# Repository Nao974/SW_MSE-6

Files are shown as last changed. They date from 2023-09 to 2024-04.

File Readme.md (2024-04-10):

# Mouse Droid MSE-6 StarWars

En collaboration avec l'association [Les Voyageur Des Etoiles] réalisation d'une réplique du **Mouse Droid MSE-6** des films **StarWars** :

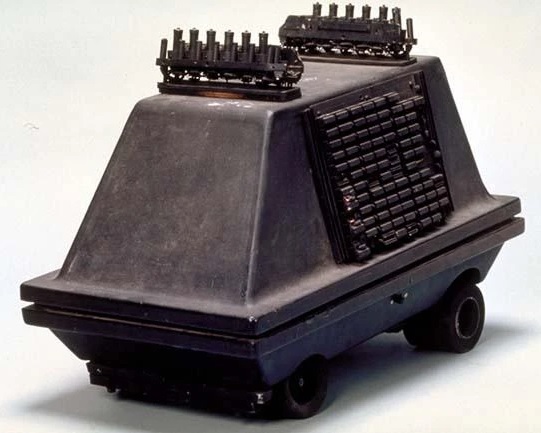
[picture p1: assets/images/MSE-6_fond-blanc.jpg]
Image du Robot
 

*Conçu et produit par Rebaxan Columni pour le compte de l'Empire. De petite taille (moins de 30cm de hauteur), il est muni de quatres roues. Ce modèle est utilisé pour les tâches de maintenance simples et pour le nettoyage des sols.*

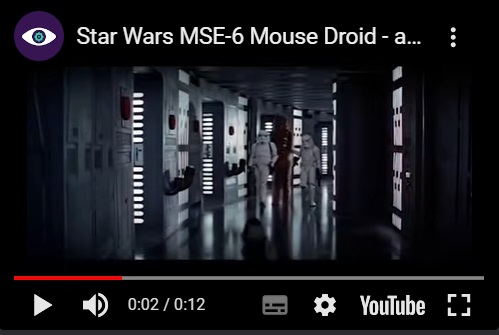
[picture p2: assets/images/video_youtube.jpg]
Video Presentation (https://youtu.be/cLqNmMH4hsg)


L'objectif du projet est d'avoir un robot pilotable par Smartphone permettant d'accompagner les acteurs dans leurs déambulations lors de salons ou d'animations.

Ce robot doit également avoir une fonction "Autonome" lui permettant de déambuler seul dans un endroit clos en évitant les obstables.

* Dimension à l'échelle 1
* Modes de fonctionnement
    * Pilotage en BlueTooth sur Android
    * Mode autonome aléatoire avec detection d'obstacles
    * Ne doit pas être très rapide car déplacement dans la foule
* Sur batterie avec une autonomie d'au moins 20 minutes
* Eclairage d'ambiance par ruban à LED
* Bruitage sonore MP3 tirés du film

# Dimensions
Plan issu du site http://luckyxero.com/droids/mouse-droid-build/ *(dimensions en inches)*

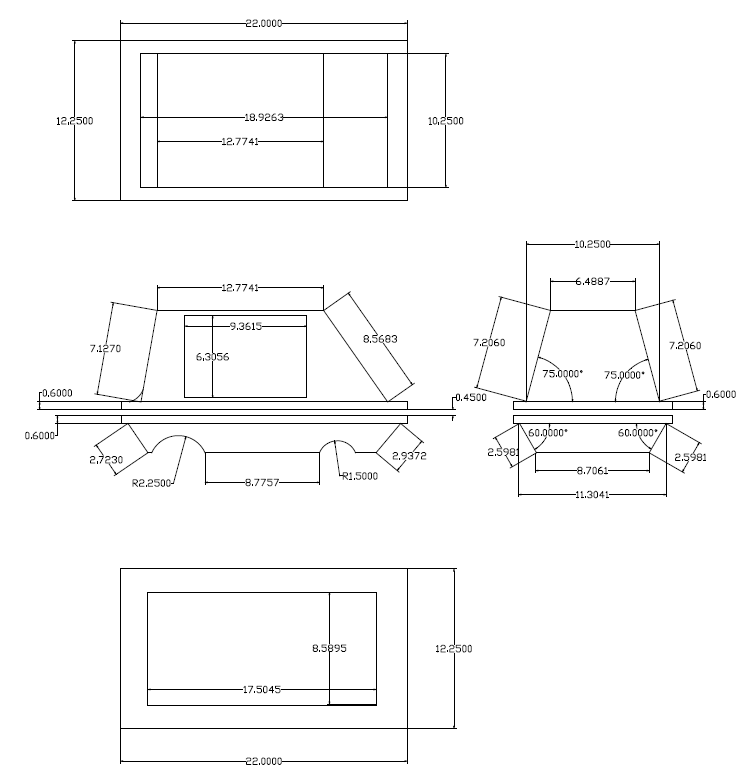
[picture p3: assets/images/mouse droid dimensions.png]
Dimension


# Construction

La coque a été fabriquée avec :
*  du carton-plume de 6 mm d'épaisseur,
* recouvert de plusieurs couches de vernis epoxy
* Peinture noire
* Décoration sur le dessus : http://www.thingiverse.com/thing:1862673
* Décoration sur les côtés : https://www.thingiverse.com/thing:916594

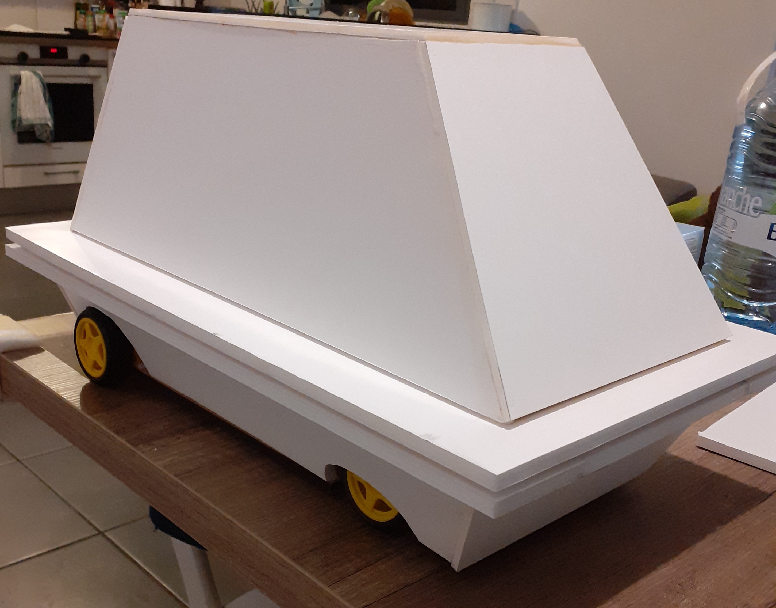
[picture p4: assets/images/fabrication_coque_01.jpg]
Construction carton plume


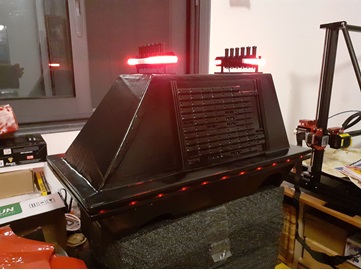
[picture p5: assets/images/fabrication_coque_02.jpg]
Avec les LEDs


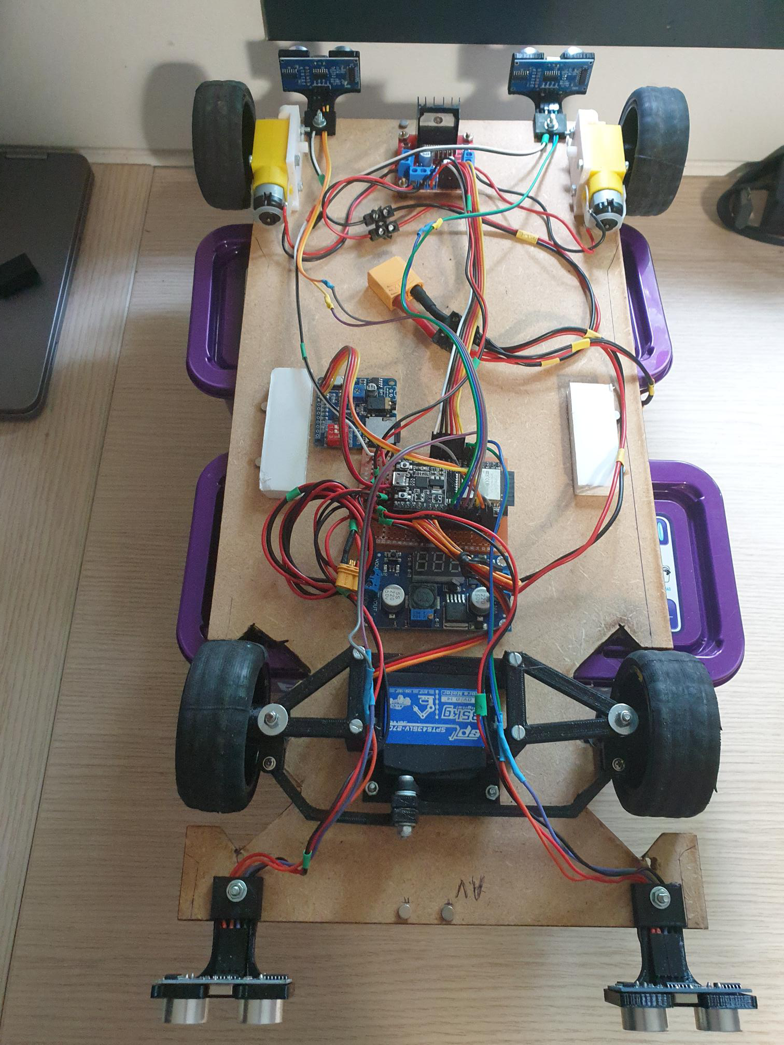
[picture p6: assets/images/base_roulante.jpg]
Base Roulante


# Pilotage par Smartphone

Télécharger l'application Android [apk]

Vous pouvez également ouvrir le projet directement dans [MIT App Inventor]

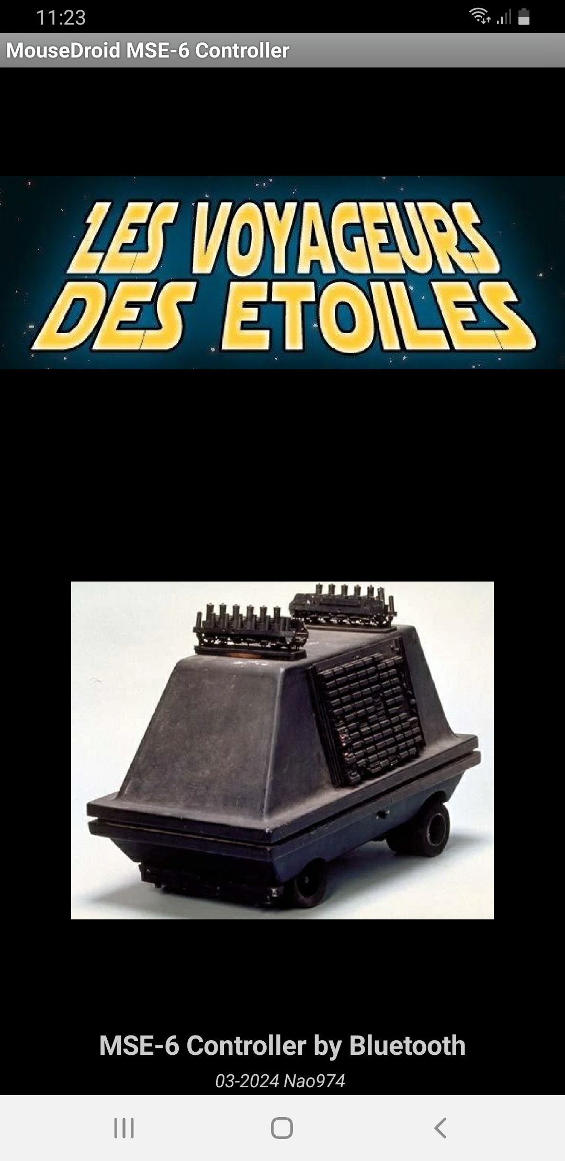
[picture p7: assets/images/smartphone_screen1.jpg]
Splash Screen
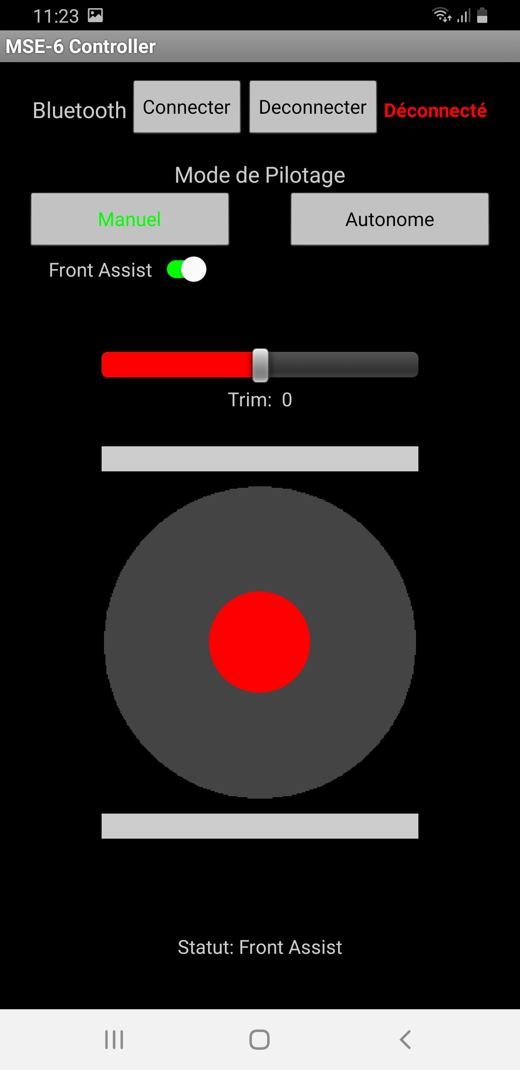
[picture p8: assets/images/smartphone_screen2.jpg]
Mode Manuel
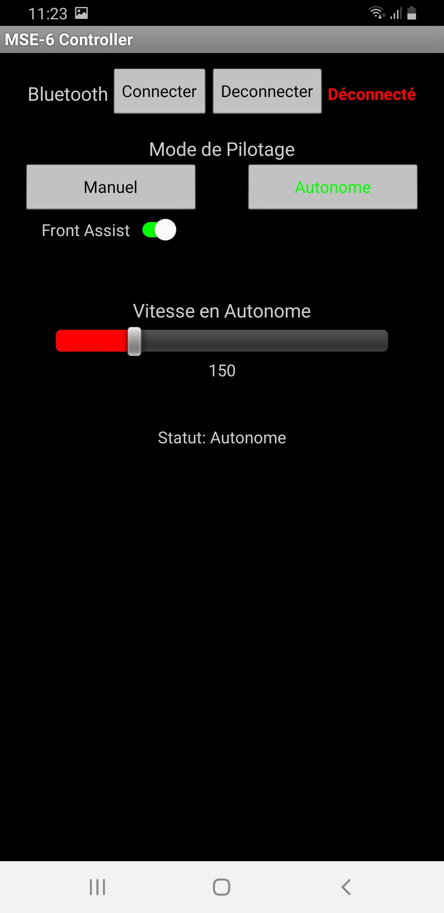
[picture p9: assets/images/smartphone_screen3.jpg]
Mode Autonome
<div align="center">&nbsp;&nbsp;</div> 

# Vidéos diverses

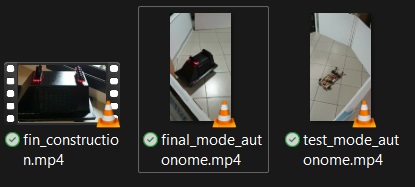
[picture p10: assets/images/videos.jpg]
Divers Vidéos


# 
*[Nao974] v1.0 2024-04*

[FICHES]: ./FICHES
[apk]: ./android_apk/MouseDroid_MSE6.apk
[MIT App Inventor]: https://gallery.appinventor.mit.edu/?galleryid=becb1436-0f10-454d-a0c5-cfbd2a7cbcf6

[Robotic974]:      https://www.facebook.com/robotic974
[Nao974]:          https://www.youtube.com/@Nao974Robotic
[Les Voyageur Des Etoiles]: https://www.facebook.com/LesVDE
[Images de référence] :     https://photos.google.com/share/AF1QipP5TdWiDbklsdGn5iPU7iJ0s8NH2A8It0JS8Ncwk7ek5rMM8T10t8TtdKYRnrsGPw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

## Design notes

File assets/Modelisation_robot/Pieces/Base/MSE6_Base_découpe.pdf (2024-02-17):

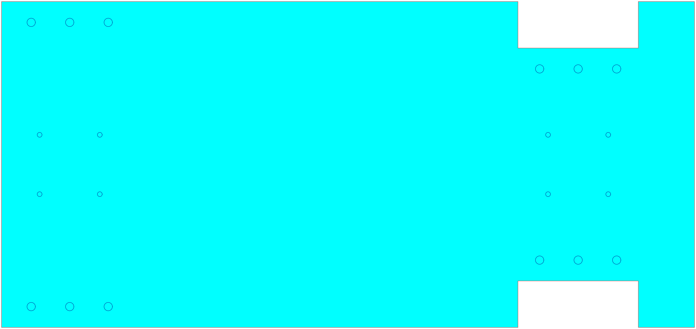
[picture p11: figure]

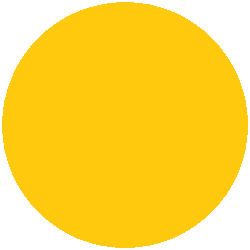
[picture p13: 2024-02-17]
assets/images/fondStickb.png

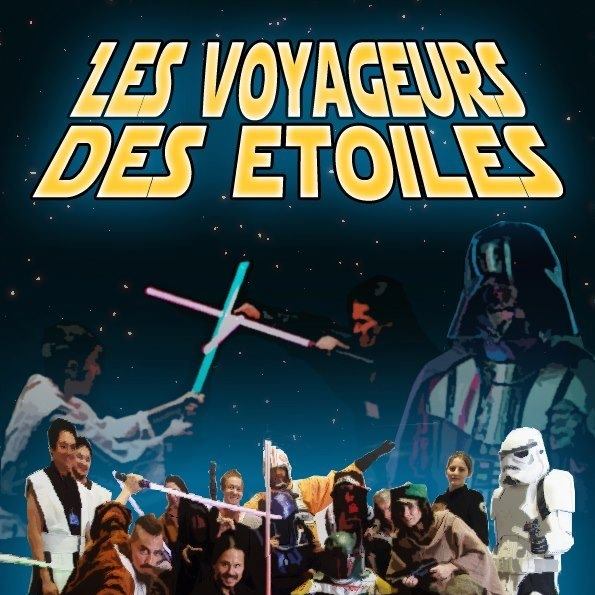
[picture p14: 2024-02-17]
assets/images/Voyageur_Etoiles.jpg

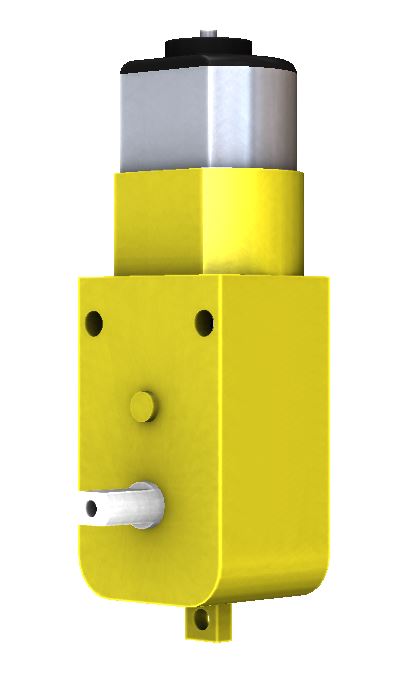
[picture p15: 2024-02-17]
assets/Modelisation_robot/Pieces/_tt-motor/motor.JPG

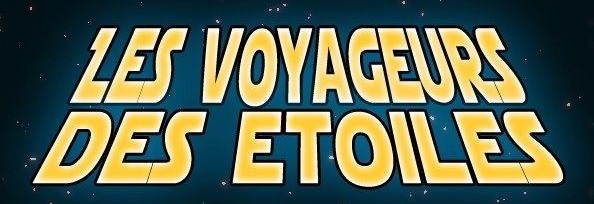
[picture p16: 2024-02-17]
assets/images/Voyageur_Etoiles_texte.jpg

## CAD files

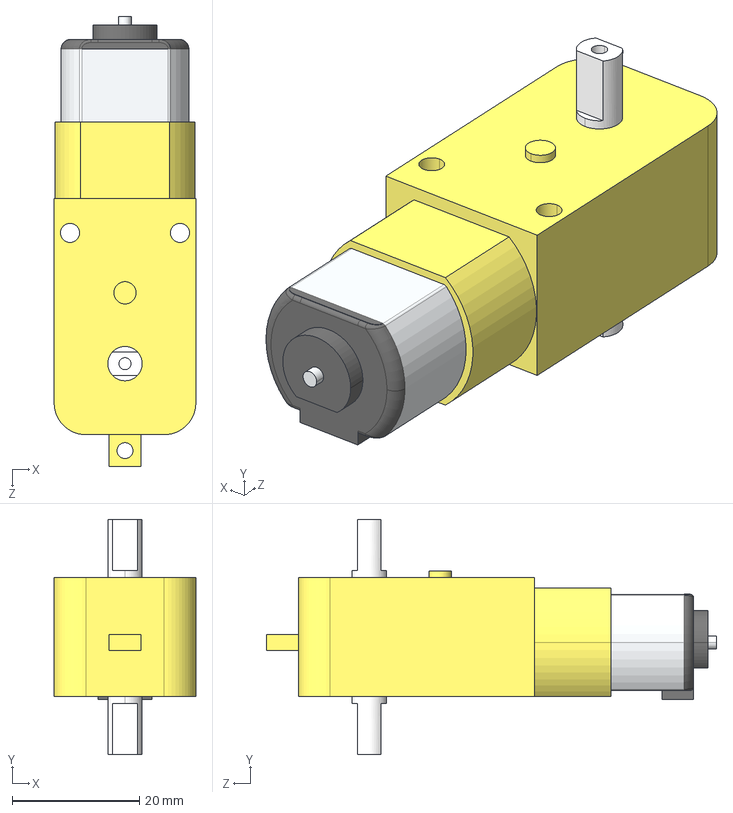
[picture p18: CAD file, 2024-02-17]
assets/Modelisation_robot/Pieces/_tt-motor/motor.STEP
22.3 x 37.0 x 70.8 mm

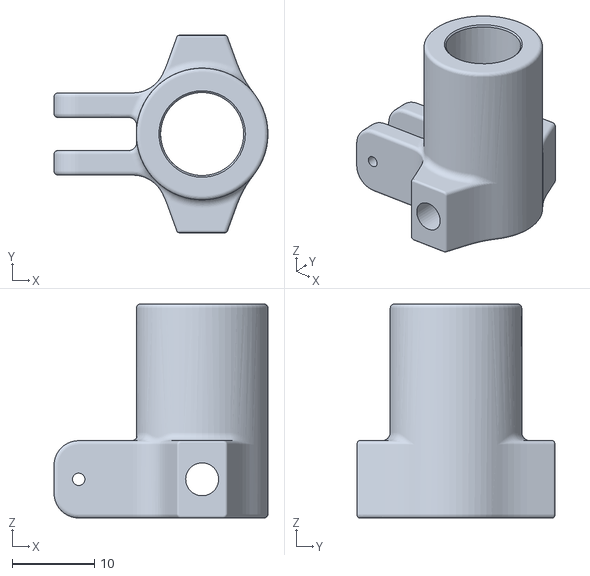
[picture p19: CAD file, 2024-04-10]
assets/Modelisation_robot/Pieces/Direction/Hub_front.STL
26.0 x 24.0 x 26.0

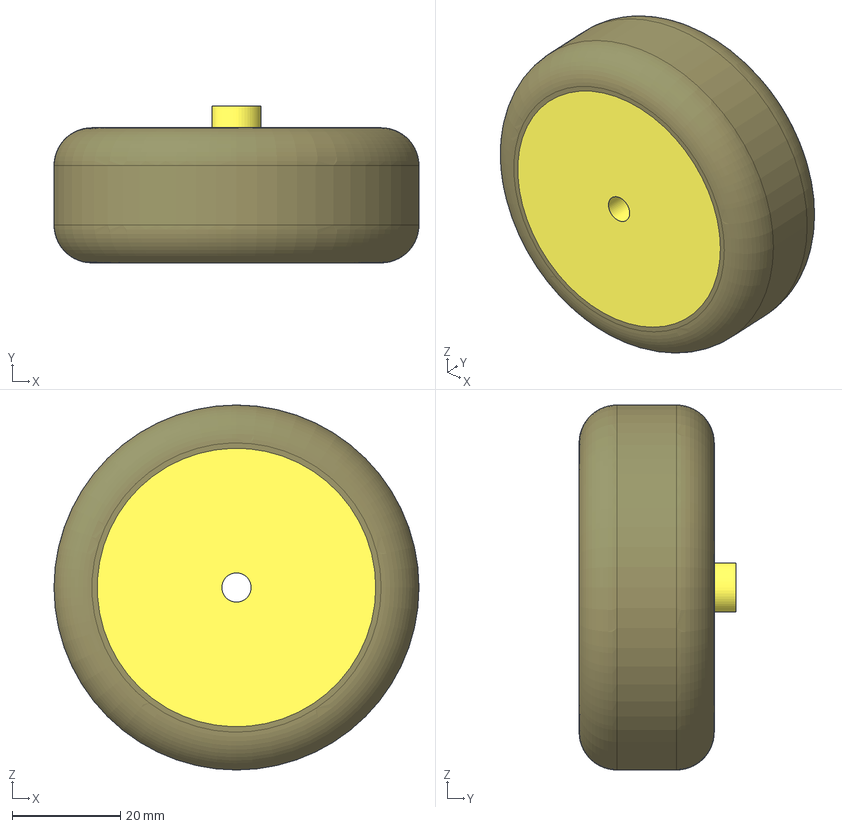
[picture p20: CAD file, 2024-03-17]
assets/Modelisation_robot/Pieces/Roue/Roue.FCStd
67.5 x 29.0 x 67.5 mm
Jante
Pneu
Binder(Roue)

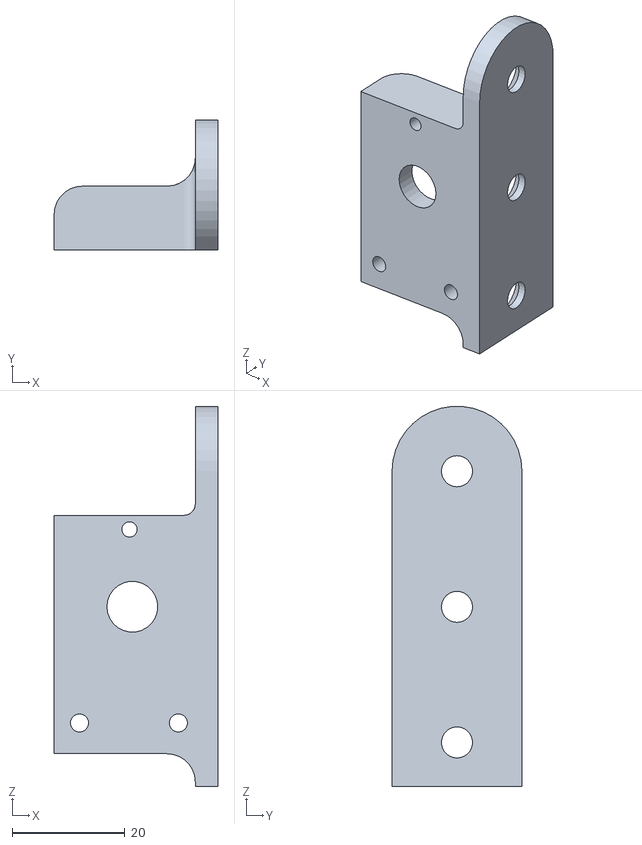
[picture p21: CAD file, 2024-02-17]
assets/Modelisation_robot/Pieces/Support_Moteur/Support_Moteur_gauche.stl
29.0 x 23.0 x 67.3

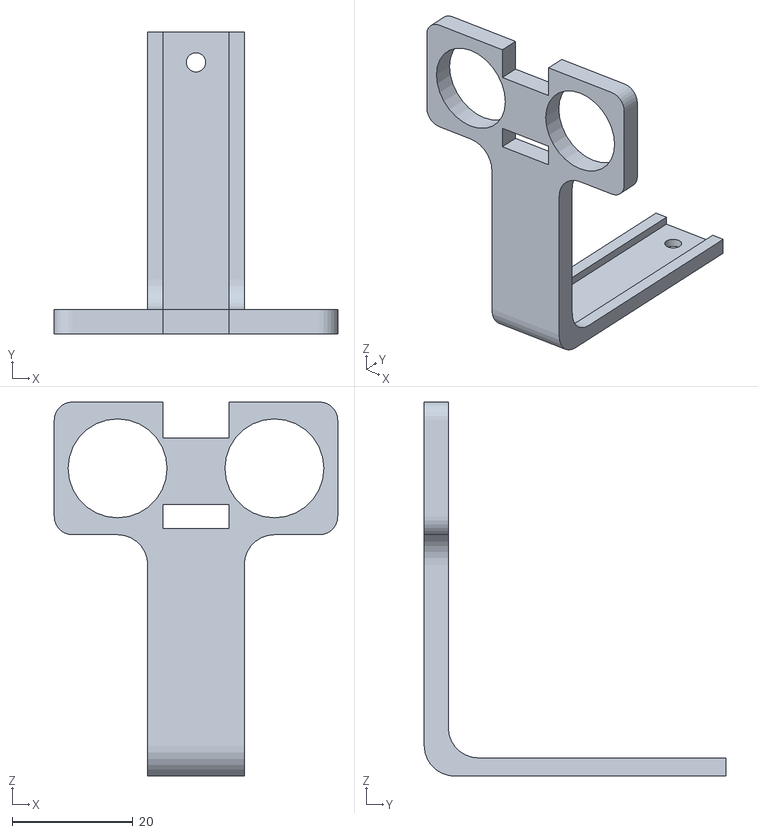
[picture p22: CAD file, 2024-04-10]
assets/Modelisation_robot/Pieces/Ultrasonic HC-SR04/support_HC-SR04_haut_arriere-Support.stl
47.0 x 50.0 x 62.0

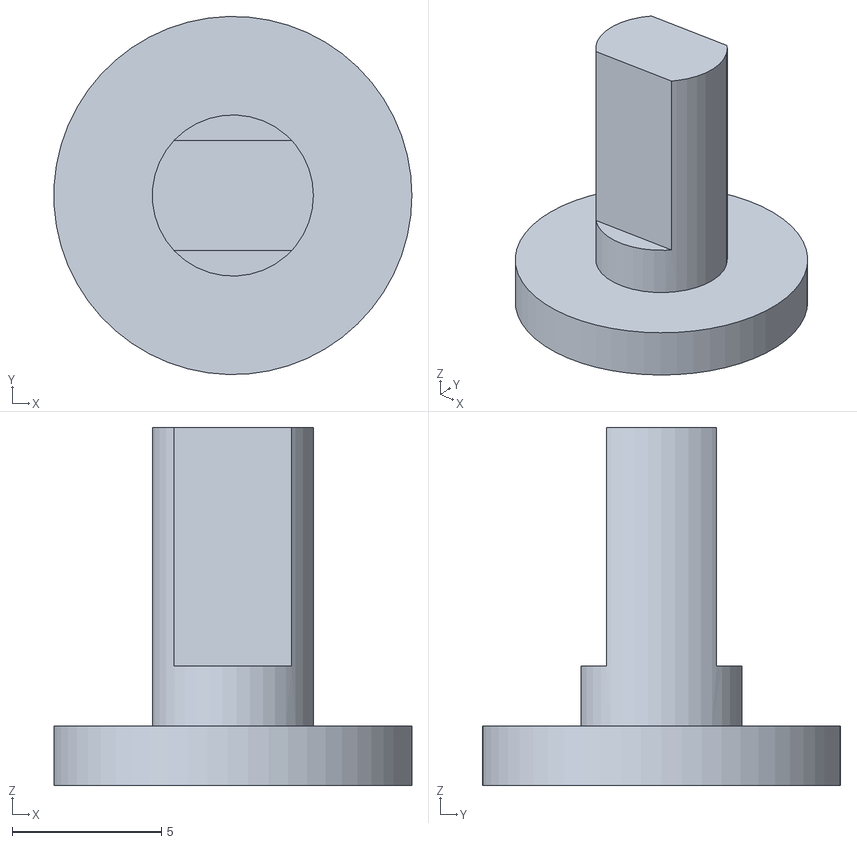
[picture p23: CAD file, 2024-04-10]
assets/Modelisation_robot/Pieces/Direction/driveshaft_front.STL
12.0 x 12.0 x 12.0

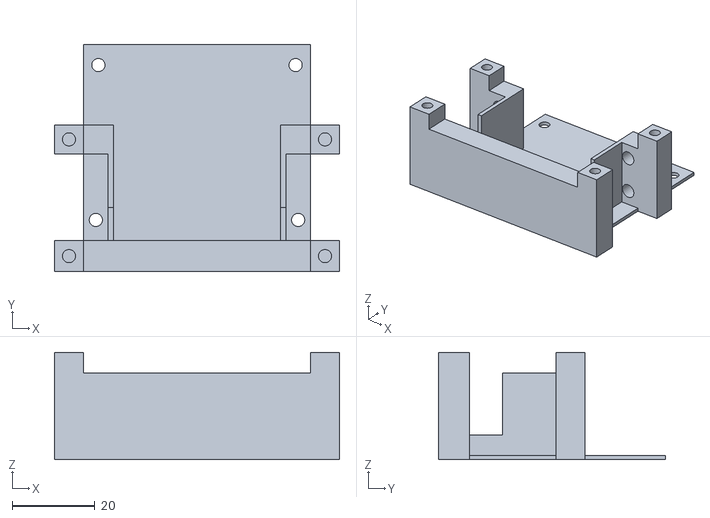
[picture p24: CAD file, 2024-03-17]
assets/Modelisation_robot/Pieces/Direction/support_servo-Body.stl
69.0 x 55.0 x 26.0

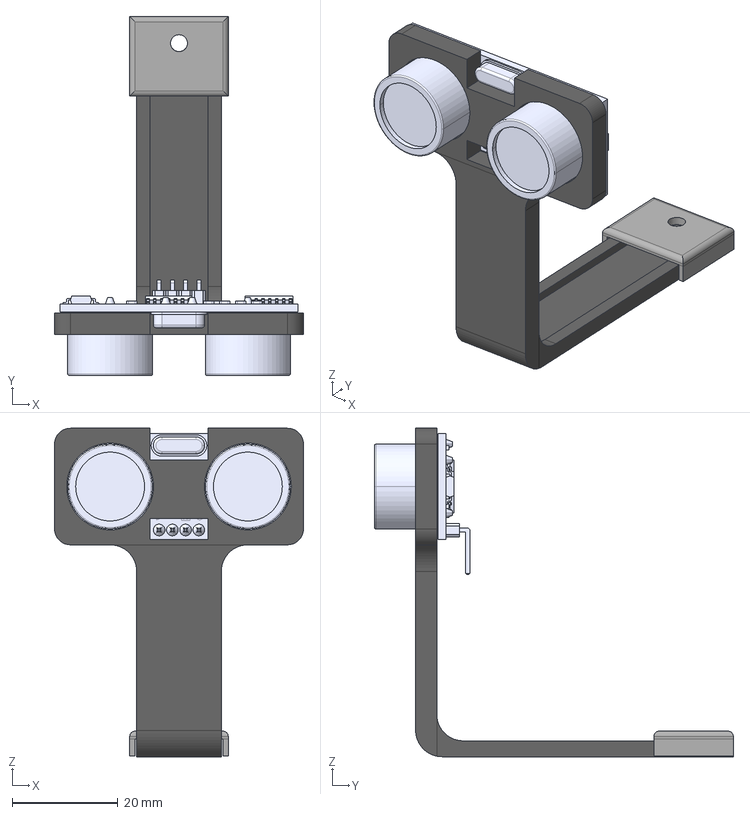
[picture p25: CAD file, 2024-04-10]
assets/Modelisation_robot/Pieces/Ultrasonic HC-SR04/support_HC-SR04_haut.FCStd
47.0 x 67.8 x 62.0 mm
Support
HCSR04 Ultrasonic Sensor
Capot vis

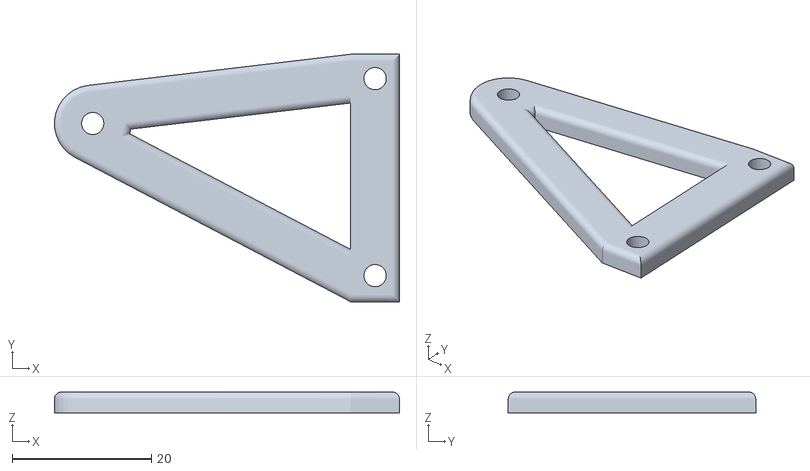
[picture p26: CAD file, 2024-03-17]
assets/Modelisation_robot/Pieces/Direction/Triangle_Gauche.stl
49.5 x 35.5 x 3.00

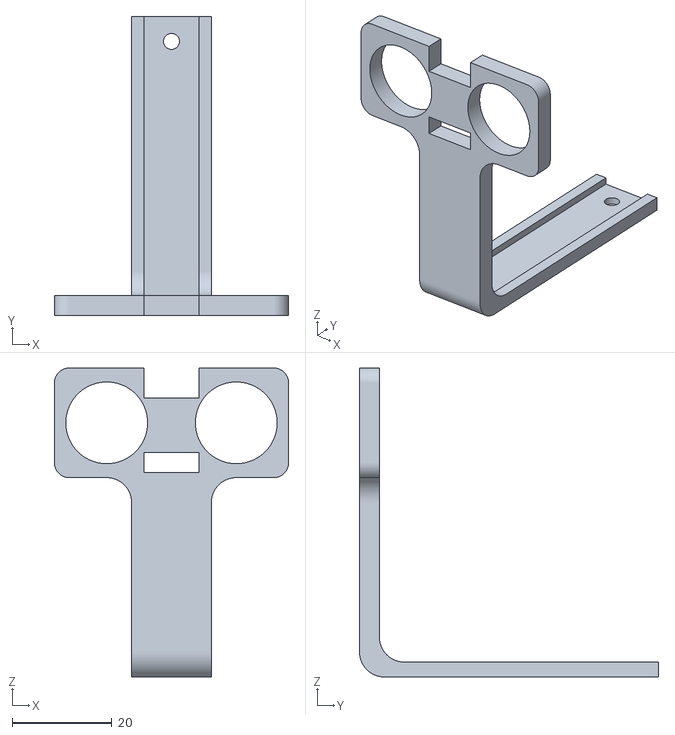
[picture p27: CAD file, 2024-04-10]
assets/Modelisation_robot/Pieces/Ultrasonic HC-SR04/support_HC-SR04_haut-Support.stl
47.0 x 60.0 x 62.0

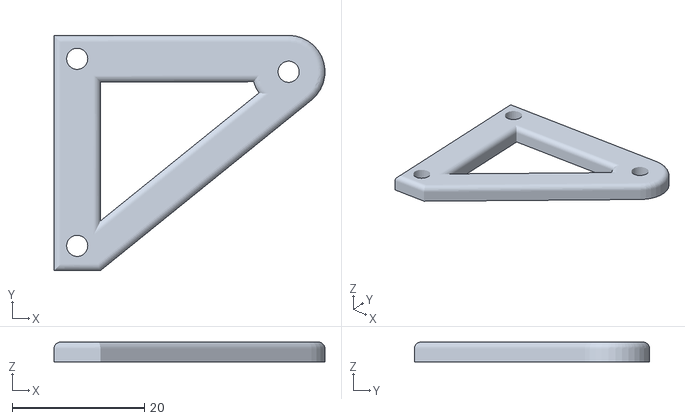
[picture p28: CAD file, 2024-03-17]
assets/Modelisation_robot/Pieces/Direction/Triangle_Droit.stl
40.9 x 35.5 x 3.00

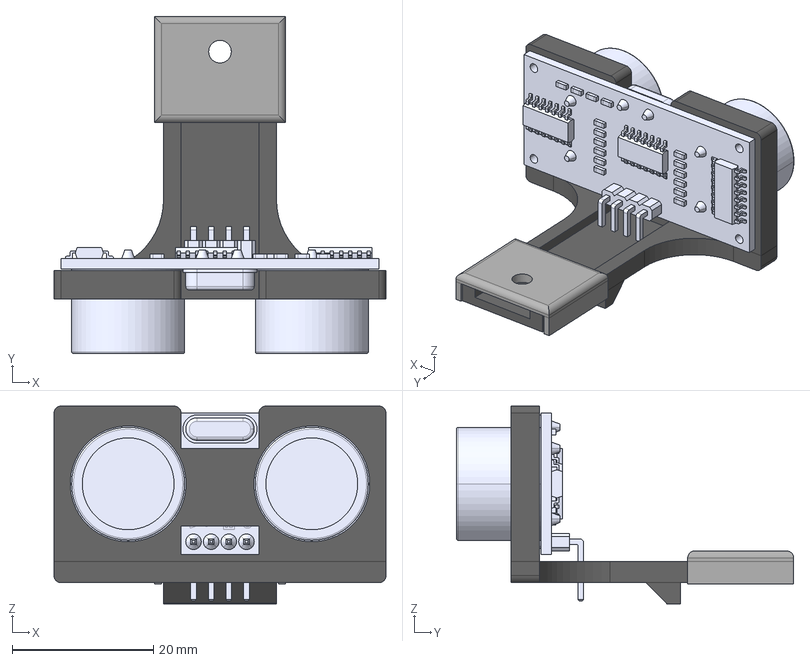
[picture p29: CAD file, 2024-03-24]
assets/Modelisation_robot/Pieces/Ultrasonic HC-SR04/support_HC-SR04_court.FCStd
47.0 x 47.8 x 28.0 mm
Support
HCSR04 Ultrasonic Sensor
Capot vis

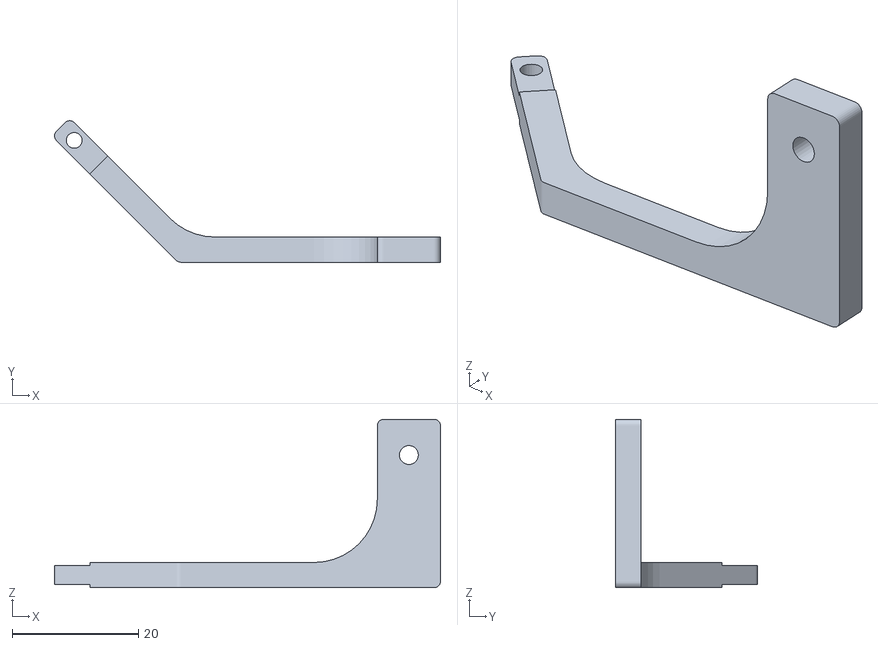
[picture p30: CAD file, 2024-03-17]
assets/Modelisation_robot/Pieces/Direction/Bras_Droit-Body.stl
61.1 x 22.4 x 26.7

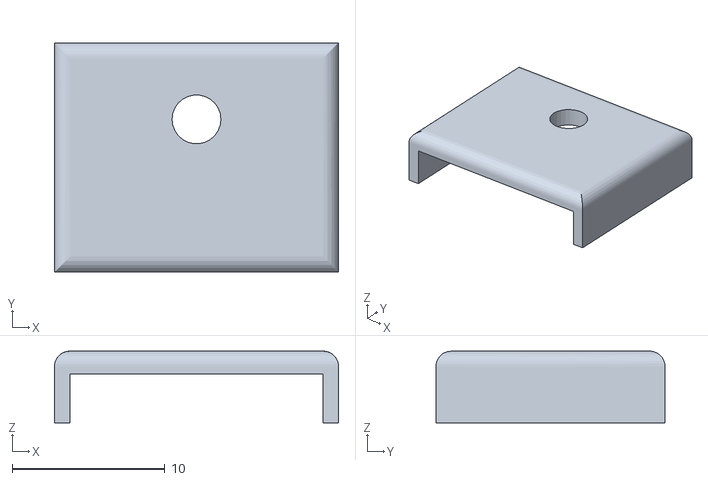
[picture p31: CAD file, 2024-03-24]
assets/Modelisation_robot/Pieces/Ultrasonic HC-SR04/support_HC-SR04_Capot vis.stl
18.6 x 15.0 x 4.70

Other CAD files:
assets/Modelisation_robot/Pieces/Support_Moteur/Support_Moteur.FCStd
assets/Modelisation_robot/Pieces/Ultrasonic HC-SR04/support_HC-SR04_haut_arriere.FCStd
assets/Modelisation_robot/Pieces/Direction/support_servo.FCStd
assets/Modelisation_robot/Pieces/Ultrasonic HC-SR04/support_HC-SR04.FCStd
assets/Modelisation_robot/Pieces/Direction/Bras_Droit.FCStd
assets/Modelisation_robot/Pieces/Direction/Bras_Gauche-Body.stl
assets/Modelisation_robot/Pieces/Direction/Bras_Gauche.FCStd
assets/Modelisation_robot/Pieces/Ultrasonic HC-SR04/HCSR04 Ultrasonic Sensor.STEP
assets/Modelisation_robot/Pieces/_tt-motor/motor.STL

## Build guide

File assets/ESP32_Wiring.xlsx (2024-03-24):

 | GPIO0 | Boot
 | GPIO1 | TX1
 | GPIO2
 | GPIO3 | RX1
 | GPIO4 | Servo Motor Direction
 | GPIO5
 | GPIO6 | Reserved SPI Flash
 | GPIO7 | Reserved SPI Flash
 | GPIO8 | Reserved SPI Flash
 | GPIO9 | Reserved SPI Flash
 | GPIO10 | Reserved SPI Flash
 | GPIO11 | Reserved SPI Flash
 | GPIO12 | Right Motor ENA
 | GPIO13
 | GPIO14 | Right Motor IN1
 | GPIO15
 | GPIO16 | US Left Back Echo
 | GPIO17 | US Left Back Trigger
 | GPIO18 | US Right Back Echo
 | GPIO19 | US Right Back Trigger
 | GPIO20
 | GPIO21 | MP3RX2
 | GPIO22 | MP3TX2
 | GPIO23 | US Right Front Trigger
 | GPIO24
 | GPIO25 | Left Motor IN2
 | GPIO26 | Left Motor IN1
 | GPIO27 | Right Motor IN2
 | GPIO28
 | GPIO29
 | GPIO30
 | GPIO31
 | GPIO32 | US Left Front Trigger
 | GPIO33 | Left Motor ENA
Input Only | GPIO34 | US Left Front Echo
Input Only | GPIO35 | US Right Front Echo
Input Only | GPIO36
 | GPIO37
 | GPIO38
Input Only | GPIO39

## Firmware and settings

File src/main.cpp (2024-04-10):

#include <Arduino.h>

// General
uint8_t drivingMode = 1, autonomousState= 1, autonomousStateLast= 1;
int16_t vitesseAutonomous;
uint32_t debugLastMillis, autonomousLastMillis, autonomousWaitLastMillis, autonomousWait;
#define DEBUG	false

#include "DYPlayerArduino.h"
const uint8_t MP3RX2 = 22;
const uint8_t MP3TX2 = 21;
DY::Player player(&Serial2);

#include "BluetoothSerial.h"
BluetoothSerial SerialBT;
int16_t btReceive[4] = {0, 0,  0, 0}; // Pilotage,  Trim, Joy X / Range Left, Joy Y / Range Right 

#include <L298N.h>
Moteur moteurGauche, moteurDroite;
int16_t vitesseBase;
int16_t reculeDuree;
int32_t reculeLastMillis;

#include "Direction.h"
#include <ESP32Servo.h>
Servo servoDir;
int16_t directionBase;

#include "Sonars.h"
#include <NewPing.h>
uint8_t sonarStatus[SONAR_NUMBER]= {0, 0, 0, 0};
NewPing sonar[SONAR_NUMBER]= {
    NewPing( 32, 34, SONAR_MAX_DISTANCE),  // Left Front sensor (trigger pin, echo pin, and max distance to ping).
    NewPing( 17, 16, SONAR_MAX_DISTANCE),  // Left Back
    NewPing( 23, 35, SONAR_MAX_DISTANCE),  // Right Front
    NewPing( 19, 18, SONAR_MAX_DISTANCE)  // Right Back
};

void setup() {
// Initialization of Serial debug
    #if DEBUG== true 
		Serial.begin(115200);
	#endif

// Initilization of the Bluetooth server
	#if DEBUG== true 
		Serial.println("SerialBT init"); 
	#endif
    SerialBT.begin("MSE-6");

// Initialization of motors
	#if DEBUG== true 
		Serial.println("Motors init"); 
	#endif
	moteurGauche.init(26, 25, 33, VITESSE_MAX); // IN1, IN2, ENA
	moteurDroite.init(14, 27, 12, VITESSE_MAX); // IN1, IN2, ENA
	vitesseBase = 0;

// Initialization Direction
	#if DEBUG== true 
		Serial.println("Servo init"); 
	#endif
	servoDir.attach(4, 1000, 2000);
	directionBase = 90;
	servoDir.write(directionBase);

// Initialization Sonars
	#if DEBUG== true 
		Serial.println("Sonars init"); 
	#endif
    sonarID = 0;
    sonarLastMillis = millis();

// Initialization MP3 Player
  Serial2.begin(9600, SERIAL_8N1, MP3RX2, MP3TX2);
  player.begin();
  player.setVolume(25); //Set the playback volume between 0 and 30. Default volume if not set: 20
  player.setCycleMode(DY::PlayMode::Random); // Play all randomly and repeat.
  player.play();

// General
	drivingMode = true; // manual control at start-up
	autonomousState = 1; //1= forward, 2= back, 3= back wait because obstacle
	vitesseAutonomous = VITESSE_MIN;
}

void loop() {

	UpdateSonars_SendBT(drivingMode);

	// if reception of data sent by bluetooth
    if ( SerialBT.available() >= 4) {
        btReceive[0] = SerialBT.read(); // Pilotage
        btReceive[1] = SerialBT.read() - 10; // Trim original value -10 to 10, send BT 0 to 20, therefore -10 to find the original value
        btReceive[2] = SerialBT.read(); // Joystick X Direction
        btReceive[3] = SerialBT.read(); // Joystick Y Vitesse

		drivingMode = btReceive[0];
		if ( drivingMode) {
			// Recalculates data in motor range
			directionBase = map(btReceive[2],250, 0, SERVO_MAX, SERVO_MIN ) + btReceive[1];
			vitesseBase = map(btReceive[3],0, 250, 255, -255 );
			#if DEBUG == true
				Serial.printf("Pilotage= %d // Trim= %d // Joy X= %d // Joy Y=%d\n", btReceive[0], btReceive[1], btReceive[2], btReceive[3]);
			#endif
		}
		else {
			vitesseAutonomous = btReceive[3];
			#if DEBUG == true
				Serial.printf("Vitesse Autonome= %s\n", vitesseAutonomous );
			#endif
		}
	}

	if ( !drivingMode ) { // autonomous mode
		autonomousStateLast = autonomousState;
		switch ( autonomousState) {
			case 1: { // Forward
				directionBase = SERVO_MIDDLE;
				vitesseBase = vitesseAutonomous;

				if ( sonarStatus[0] == 1 ) { // Left Front
					directionBase = SERVO_DROITE;
				}
				if ( sonarStatus[2] == 1 ) {// Right Front
					directionBase = SERVO_GAUCHE;
				}
				if ( sonarStatus[0] == 2 || sonarStatus[2] == 2 )  {
					autonomousState = 2;
					autonomousLastMillis = millis();
					autonomousWait = 0;
				}
				break;
			}
			case 2: { // go back
				if ( millis() > autonomousLastMillis+ autonomousWait + 2000)
					autonomousState = 1;
				else {
					directionBase = SERVO_DROITE;
					vitesseBase = -vitesseAutonomous;
					if (sonarStatus[1] == 2 || sonarStatus[3] == 2) { // obstacle at the back
						vitesseBase = 0;
						autonomousWaitLastMillis = millis();
						autonomousState = 3;
					}
				}
				break;
			}
			case 3: { // obstacle at the back, we wait
				if (sonarStatus[1] != 2 && sonarStatus[3] != 2) {
						autonomousWait = autonomousWait + ( millis() - autonomousWaitLastMillis );
						autonomousState = 2;
					}
				else if ( millis() > autonomousLastMillis + 2500 )
					autonomousState = 1;
			}
		}
		if ( autonomousStateLast != autonomousState) {
			SerialBT.print("9");
            SerialBT.println(autonomousState); 
		}

	}
	#if DEBUG == true
		if ( millis() > debugLastMillis+ 500) {
			Serial.printf("Vitesse base= %d, direction base=%d \n",vitesseBase,directionBase);
			debugLastMillis = millis();
		}
	#endif
	turnSecureMode(directionBase);
	if ( drivingMode == 2 ) {
		if ( ( sonarStatus[0] == 2 || sonarStatus[2] == 2) && vitesseBase > 0 )
			vitesseBase = 0;
		if ( ( sonarStatus[1] == 2 || sonarStatus[3] == 2) && vitesseBase < 0 )
			vitesseBase = 0;
			}
	moteurGauche.speed(vitesseBase);
	moteurDroite.speed(vitesseBase);
}

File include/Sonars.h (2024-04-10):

#include <Arduino.h>
#include <NewPing.h>
#include "BluetoothSerial.h"

const uint16_t SONAR_MAX_DISTANCE = 2000; // Maximum distance (in cm) to ping.
const uint16_t SONAR_LIMIT_ORANGE = 60; // in cm
const uint16_t SONAR_LIMIT_RED = 30; // in cm
const uint8_t SONAR_NUMBER = 4;
const uint16_t SONAR_INTERVAL = 100; // Wait 50ms between pings (about 20 pings/sec). 29ms should be the shortest delay between pings.
uint16_t sonarDistance = 0;
uint8_t sonarID = 0;         
uint32_t sonarLastMillis = 0;  

extern uint8_t sonarStatus[SONAR_NUMBER];
extern NewPing sonar[SONAR_NUMBER];
extern BluetoothSerial SerialBT;

void UpdateSonars_SendBT(const uint8_t sendBT) {
    if ( millis() > sonarLastMillis + SONAR_INTERVAL) { 
        sonarDistance = sonar[sonarID].ping_cm();
        if ( sonarDistance < 2) sonarDistance = 255;

        if ( sonarDistance <= SONAR_LIMIT_RED ) {
            if ( sonarStatus[sonarID] != 2 ){
                sonarStatus[sonarID] = 2;
                if (sendBT) {
                    SerialBT.print(sonarID);
                    SerialBT.println("2");
                }
            }
        }
        else if ( sonarDistance <= SONAR_LIMIT_ORANGE ){
            if ( sonarStatus[sonarID] != 1 ) {
                sonarStatus[sonarID] = 1;
                if (sendBT) {
                    SerialBT.print(sonarID);
                    SerialBT.println("1"); 
                }
            }
        }
        else if ( sonarStatus[sonarID] != 0) {
                sonarStatus[sonarID] = 0;
                if (sendBT) {
                    SerialBT.print(sonarID);
                    SerialBT.println("0");   
                }           
        }

        #if DEBUG == true
            {Serial.print(sonarID);Serial.print(": ");Serial.println(sonarDistance);}
        #endif

        sonarID = ++sonarID % SONAR_NUMBER;
        sonarLastMillis = millis();
    }
}

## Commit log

2023-09-14 Change board
2023-09-14 add recalculate motor range
2023-09-14 motors tests
2023-09-24 Add MP3 & update pin RX & TX
2023-10-01 test mp3
    [BoM.xlsx]
2024-01-14 update files
    [Roue.FCStd, Support_Moteur.FCStd, Support_Moteur_gauche.stl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]
2024-02-13 Add ESP32 Wiring + Test Sonar Ping
    [ESP32_Wiring.xlsx, HCSR04 Ultrasonic Sensor.STEP, Tension-Courant-Conso.xlsx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]
2024-02-17 First test
    [support_HC-SR04-Support.stl, support_HC-SR04.FCStd]
2024-02-17 Test Ultrasonics OK
2024-02-19 Update asset 3D models and wiring
    [ESP32_Wiring.xlsx, support_HC-SR04-Capot vis.stl, support_HC-SR04-Support.stl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]
2024-02-19 Start of motor test
2024-02-23 test motor
2024-03-12 Test motor with new battery
2024-03-17 final Sonar test with color-coded feedback
2024-03-17 Update 3D models
    [Bras_Droit-Body.stl, Bras_Droit.FCStd, Bras_Gauche-Body.stl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]
2024-03-17 Test Sonar with BT
2024-03-24 Update Assets
    [support_HC-SR04_court-Capot vis.stl, support_HC-SR04_court-Support.stl, support_HC-SR04_court.FCStd]
2024-03-24 Add Sonars Back
    [ESP32_Wiring.xlsx]
2024-03-24 Include New Sonar Lib in Main and refactoring
2024-03-24 Add sonar Controle from Speed in driving mode
